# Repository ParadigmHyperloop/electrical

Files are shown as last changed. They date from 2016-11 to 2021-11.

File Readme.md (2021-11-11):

# Electrical System for the Paradigm Hyperloop Pod

## Quick Start

All boards are built using KiCad EDA (http://kicad.org/).  It is free and open source software!

1. Download and Install KiCAD
2. Clone this Repo
3. Checkout a new branch or your branch other than master
3. Open the project file (.pro) for the board you are interested in
4. Make any edits, create a branch, add and commit the changes to git, then push. 

## Organization

All files for the current revision should be kept in folders in the root directory.
All files for a completed revision should be kept in folders in the appropriate "RevX" sub-directory.
Still not sure how we will handle when some boards need to be revved but not others...

## Ops Roadmap

There are a number of nice-to-have features that will streamline the electrical workflow of board
design. The following features employ a CI server that minicks some of the features that the software
team enjoys in their git workflow.

- Automatic DRC when the PR is opened. Gate PRs on passing DRC.
- Whenever A new PR is merged to `master`, a bot will pull `master` and do the following, and commit the changes back to `master`
  - Automatic PDF export and storage in `./<board>/PDFs/`
  - Automatic BOM export and storage as `./<board>/BOM.csv`
  - Automatic SVG export and storage in `./<board>/SVG/`
  - Automatic 3D Viewer export and storage in `./<board>/3D/`
  - Automatic DRC report and storage in `./<board>/reports/`
  - Automatic export of gerbers and drill files per spec file.  Storage in `./<board>/mfg/`
  - Automatic Generation of `./board/BOT.version` containing the SHA of the commit that everything was generated for 

# License

See the [LICENSE](LICENSE) for full licensing details.

In summary, (you still need to read the whole thing), these boards are for Paradigm, 
and Paradigm only. It is shared with the world for the benefit of observers and 
potential Paradigm team members. If you wish to utilize these designs in any
way, you must contact us first and receive written permission to utilize the
designs for the purpose you require. 

We don't want to be restrictive, and we will almost certainly grant you permission,
but we want to know what you are using our designs for, and we want to make sure
you are using them correctly and safely.

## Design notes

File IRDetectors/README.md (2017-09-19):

# About this Board

* **Owner:** @edhurtig
* **Status:** `Build`
* **Topic:** Research

## Design Abstract 

In the most basic sense, this board is an Arduino with support for 2 modulated IR emitters and paired receivers. They are essentially smart IR proximity sensors. 

## Purpose

These boards are intended to detect vertical strips (4" wide) that are placed every 100' on the hypertube walls. These strips are useful for navigation purposes and tell the pod where it is in the tube.

These boards are also somewhat of a prototype for a localized control module for subsystems like #brakes where a local uC receives commands from the main flight computer, but locally is the one responsible for controlling the state of the brake control solenoids, monitoring pressures and temperatures, etc.

## Tech Specs

- **Microcontroller** Atmega32U4
- **Communication** 1 Micro USB, 1 ISP Header, 1 RS485 bus, I2C, (maybe) CANbus
- **Sensors** 2 IR Emitters, 2 IR Receivers. Local hardware-based 36Khz IR modulator.
- **Expansion Headers** All unused Atmega inputs and outputs routed to an expansion header

### RS485 Details
There are 3 ports that all share the RS485 connection: 2x Ethernet jacks (for daisy chain), 1x 4 pin Phoenix contact port

### Power Details

This board is a 5V logic level board. The board may be powered over USB or via an external power source. The external power source is recommended at 5.5V. Do not exceed 12V on any of the external power inputs.

### External Power Inputs

Power may be supplied through the 2 pin Phoenix Contact Power Connector as labeled on the board's silkscreen.

Alternatively, power may be supplied via the RJ45 jacks by supplying 5.5-12V on pin 8, and Ground on pin 7.  The jumpers for VCOM power and VCOM GND must be stuffed in order to enable power via the Ethernet ports.

**Do not plug these boards into a standard ethernet switch, behavior is undefined**

### On-Board Documentation (Silkscreen)
```
5V Logic
VCC Regulated 5V
VCOM Recommended 5.5V

Ethernet Pinout:
1-2: RS485 RX - / +
3: External IR Sync
4-5: RS485 TX - / +
6: Passthrough
7: VCOM - (Ground)
8: VCOM + (5-12V DC)

VCOM PWR set jumpers 
GND EN & VCOM EN 
```
## Status

- **Rev 1A** was ordered and lost in transit 😢 
- **Rev 1B** was ordered and partially assembled. The first board is currently in a state were it powers on. Next step is to plug in an ISP and flash a bootloader onto the Atmega.

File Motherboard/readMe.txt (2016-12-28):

Notes for Motherboard files.

*** Schematic ***
BBB headers will be shown true to pins because pinouts are not 
   set and updating the headers will be annoying.

Signals for MUX pins will be denoted with labels instead of wire 
   connections for flexibility and cleanliness.     

*** hyperLib ***
A and B designator for CD74HC4067 designate pinout orientation
   A is true to the physical pins, B is to show purpose/flow.

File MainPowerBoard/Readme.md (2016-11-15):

# Main Power Board
This board provides approriate conversion of power from 120/240VAC and 37V nominal battery packs and distribution to both 24V and 5V system loads (all loads).

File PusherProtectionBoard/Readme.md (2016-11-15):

# Emergency Power Board
This board is placed near the backup battery pack. It's purpose is, in the case of a full electrical system failure, to drain the high pressure line, confirm it is drained, and activate the emergency brakes if the pod is not currently being pushed.

## Interface
The inputs to this board are the transducer for the high pressure line (wired in parallel to its connection to BBB), the combined battery voltage from the Main Power Board, and the sensor for when the pusher is pushing (from the push plate on the rear of the pod). The outputs are a connection to the high pressure solenoid and connections to the e-brake solenoids.

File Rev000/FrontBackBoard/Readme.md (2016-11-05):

# Front/Back Board of Pod

One board is duplicated in both locations, in an effort to distribute the power system

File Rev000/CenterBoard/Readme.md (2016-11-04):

# Center Board of Pod

This board houses the main power management system, taking in 36V from the battery and distributing 24V and 5V rails to other boards throughout the pod

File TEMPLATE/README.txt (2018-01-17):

README:
I have not found a convenient way to save and load template field names for components. 
for now do the following: open kiCAD -> preferences -> Template Field Names. Then add:

Manufacturer
MFG. P/N
Vendor
Vendor P/N
Tolerance (%)

All default values should be blank, except DigiKey. 
All should be invisible except Tolerance

*Change your default text size to 41 mil

****
To load the template into the test project:
click on the Page settings via GUI or file->page settings. Click 
"browse" at the bottom and find the .wks file.

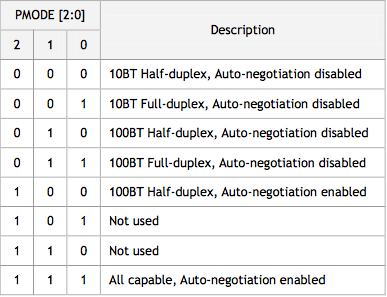
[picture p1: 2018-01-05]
Node/W5500_PMODE_settings.png

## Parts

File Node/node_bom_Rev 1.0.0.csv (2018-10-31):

Component | Description | Part | References | Value | Footprint | Quantity Per PCB | Datasheet | Digikey P/N | Mfg. Part Num | Vendor Part Num | Vendor Name | Mfg. Name | Vendor | Vendor P/N | MFG. P/N | Manufacturer | Package | MP | Stuffing | Tolerance | Manufacturer P/N | Mfr P/N
1 |  | C_small | C909 C1502 C1505 C1507 C1508 C1509 C1510 C1512 C1513 C1515 C1516 | 0.1uF | C_0805_HandSoldering | 11
2 |  | C | C205 C219 C220 C221 C222 C223 C224 C1305 C1307 C1308 C1401 C1403 C1404 C1518 C1520 C1521 C1601 C1603 C1604 C1702 C1708 C1710 C1711 C1801 C1803 C1804 C2304 C2305 C2308 C2310 | 100nF | C_0805_HandSoldering | 30 |  | 311-1088-1-ND
3 |  | C_large | C405 C506 | 100nF | C_0805_HandSoldering | 2 |  |  | GMK212BJ104KGHT | 587-3364-1-ND | Digi-Key | Taiyo Yuden
4 |  | C_small | C1503 C1506 | 100uF | C_0805_HandSoldering | 2
5 |  | C | C209 C210 | 10nF | C_0805_HandSoldering | 2
6 |  | C_large | C505 | 10pF | C_0805_HandSoldering | 1 |  |  | C0805C100K5GACTU | 399-7975-1-ND | Digi-Key | Kemet
7 |  | C | C218 C2302 C2309 | 10uF | C_0805_HandSoldering | 3
8 |  | C_small | C902 | 10uF | C_0805_HandSoldering | 1
9 |  | C_large | C504 | 12nF | C_0805_HandSoldering | 1 |  |  | CL21B123KBANNNC | 1276-2454-1-ND | Digi-Key | Samsung
10 |  | C_small | C905 | 150pF | C_0805_HandSoldering | 1
11 |  | C | C2303 C2307 | 15pF | C_0805_HandSoldering | 2
12 |  | C_large | C602 C702 | 15pF | C_0805_HandSoldering | 2 |  |  | CC0805JRNPO9BN150 | 311-1101-1-ND | Digi-Key | Yageo
13 |  | C | C202 C203 | 18pF | C_0805_HandSoldering | 2
14 |  | C | C1201 C1306 C1402 C1519 C1602 C1707 C1709 C1802 | 1uF | C_0805_HandSoldering | 8 |  | 1276-1946-1-ND
15 |  | C_large | C508 C601 C603 C701 C703 | 1uF | C_0805_HandSoldering | 5 |  |  | GRT21BC81E105KE13L CC0805KRX5R7BB105 | 490-12351-1-ND 311-3427-1-ND | Digi-Key | Murata Yageo
16 |  | C_small | C901 C903 C904 C906 C907 C908 | 1uF | C_0805_HandSoldering | 6
17 |  | C_large | C401 | 2.2uF | C_1206_HandSoldering | 1 |  |  | C3216X7S2A225K160AB | 445-5207-1-ND | Digi-Key | TDK
18 |  | C_large | C501 C502 | 2.2uF | C_0805_HandSoldering | 2 |  |  | C2012X7R1H225K125AC | 445-5968-1-ND | Digi-Key | TDK
19 |  | C_large | C404 | 2.4nF | C_0805_HandSoldering | 1 |  |  | GRM2165C1H242JA01D | 490-1629-1-ND | Digi-Key | Murata
20 |  | C_large | C402 C503 | 2.7nF | C_0805_HandSoldering | 2 |  |  | CC0805KRX7R9BB272 | 311-1130-1-ND | Digi-Key | Yageo
21 |  | C | C2301 C2306 | 22pF | C_0805_HandSoldering | 2
22 |  | C_large | C406 C407 | 22uF | C_0805_HandSoldering | 2 |  |  | C2012X5R1V226M125AC | 445-14428-1-ND | Digi-Key | TDK
23 |  | C | C2201 | 4.5nF | C_0805_HandSoldering | 1
24 |  | C | C211 | 4.7uF | C_0805_HandSoldering | 1
25 |  | C_large | C507 | 47uF | C_1206_HandSoldering | 1 |  |  | CL31A476MPHNNNE | 1276-3063-1-ND | Digi-Key | Samsung
26 |  | C | C207 C208 | 6.8nF | C_0805_HandSoldering | 2
27 |  | C_large | C403 | 82pF | C_0805_HandSoldering | 1 |  |  | CL21C820JB61PNC | 1276-2695-1-ND | Digi-Key | Samsung
28 |  | C | C1001 C1002 C1003 C1004 C1101 C1102 C1301 C1302 C1303 C1304 | C | C_0805_HandSoldering | 10
29 |  | C_large | C604 C704 | C | C_0805_HandSoldering | 2
30 |  | D_Zener_ALT | D404 | 20V | D_SOD-323_HandSoldering | 1 |  |  | MM3Z20VT1G | MM3Z20VT1GOSCT-ND |  | ON Semi
31 |  | D_Zener_ALT | D403 | 25V | D_SOD-123 | 1 |  |  | MMSZ4710T1G | MMSZ4710T1GOSCT-ND | Digi-Key | ON Semi
32 |  | D_Zener_ALT | D702 | 3.6V | D_SOD-323_HandSoldering | 1 |  |  | MM3Z3V6T1G | MM3Z3V6T1GOSCT-ND | Digi-Key | ON Semi
33 |  | D_Zener_ALT | D503 D602 | 6V | D_SOD-123 | 2 |  |  | MMSZ5233B-TP | MMSZ5233B-TPMSCT-ND | Digi-Key | Micro
34 |  | DIODESCH | D401 | DIODESCH | D_SMC_Handsoldering | 1 |  |  | B560C-13-F | B560C-FDICT-ND | Digi-Key | Diodes
35 |  | DIODESCH | D501 | DIODESCH | D_SMB_Handsoldering | 1 |  |  | B140B-13-F | B140B-FDICT-ND | Digi-Key | Diodes
36 |  | LED | D402 D502 D601 D701 | GRN | LED_1206_HandSoldering | 4 |  |  | APT3216LZGCK | 754-1944-1-ND | Digi-Key | Kingbright
37 |  | Fuse | F1101 F1102 | Fuse | R_1206_HandSoldering | 2 |  |  | C1Q 250 | 507-1073-1-ND |  | Bel Fuse
38 |  | Fuse | F1601 | Fuse | R_1812_HandSoldering | 1 |  |  | MF-MSMF050-2CT-ND | MF-MSMF050-2 |  | Bourns
39 | Generic connector, single row, 01x02 | Conn_01x02 | J301 J1501 J1502 J1503 J1504 J1505 J1506 J1507 J1508 | CONN_01X02 | Molex_2pin_power_0010844022 | 9 |  |  |  |  |  |  | DigiKey | WM1263-ND | 0010844022 | Molex, LLC Molex LLC
40 | Generic connector, single row, 01x02 | Conn_01x02 | J302 J303 | CONN_01X02 | Pin_Header_Straight_1x02_Pitch2.54mm | 2 |  |  |  |  |  |  | DigiKey | S7000-ND | PPTC021LFBN-RC | Sullins Conn. Solutions
41 | Generic connector, single row, 01x04 | Conn_01x04 | J1509 J1510 | CONN_01X04 | Molex_4pin_power_10-84-4042 | 2 |  |  |  |  |  |  | DigiKey | WM1265-ND | 10-84-4042 | Molex Connector Corporation
42 | Generic connector, single row, 01x03 | Conn_01x03 | J1001 J1002 J1003 J1004 J1101 J1102 J1201 J1202 J1203 J1204 J1205 J1206 J1900 J1901 J1902 J1903 | Conn_01x03 | TE_3_pos_header_640456-3 | 16 |  |  | 640456-3 | A19470-ND |  | TE Connectivity
43 | Generic connector, double row, 02x01, this symbol is compatible with counter-clockwise, top-bottom and odd-even numbering schemes. | Conn_02x01 | J802 J803 | Conn_02x01 | Pin_Header_Straight_2x01_Pitch2.54mm | 2 |  |  |  |  |  |  | DigiKey | 952-2262-ND | M20-9990246 | Harwin Inc
44 | Generic connector, double row, 02x02, odd/even pin numbering scheme (row 1 odd numbers, row 2 even numbers) | Conn_02x02_Odd_Even | J801 | Conn_02x02_Odd_Even | Pin_Header_Straight_2x02_Pitch2.54mm | 1 |  |  |  |  |  |  | DigiKey | 609-3242-ND | 67997-404HLF | Amphenol FCI
45 | Generic connector, double row, 02x03, odd/even pin numbering scheme (row 1 odd numbers, row 2 even numbers) | Conn_02x03_Odd_Even | J1601 | Conn_02x03_Odd_Even | Pin_Header_Straight_2x03_Pitch2.54mm | 1 |  |  |  |  |  |  | DigiKey | S9015E-03-ND | GRPB032VWVN-RC | Sullins Conn. Solutions
46 | Generic connector, double row, 02x05, odd/even pin numbering scheme (row 1 odd numbers, row 2 even numbers) | Conn_02x05_Odd_Even | J2201 | Conn_02x05_Odd_Even | Pin_Header_Straight_2x05_Pitch1.27mm | 1 |  |  |  |  |  |  | DigiKey | 609-3712-ND | 20021111-00010T4LF | Amphenol FCI
47 |  | RB1-125BAG1A | J201 | RB1-125BAG1A | WIZNET_RB1-125BAG1A | 1 | 2.18 USD |  | RB1-125BAG1A |  |  | WIZnet |  |  |  |  | HVQFN-36 NXP Semiconductors | RB1-125BAG1A
48 | USB Micro Type B connector | USB_B_Micro | J1602 | USB_B_Micro | USB_Micro-B_10103594-0001LF | 1 |  |  | 609-4050-1-ND | 10103594-0001LF |  | Amphenol
49 |  | L_large | L401 | 33uH | Wurth_inductor_7443551331 | 1 |  |  | 7443551331 | 732-3881-1-ND | Digi-Key | Wurth Electronics
50 |  | L_large | L501 | 33uH | Bourns_33uH_inductor_SRR6028-330Y | 1 |  |  | SRR6028-330Y | SRR6028-330YCT-ND | Digi-Key | Bourns
51 |  | Ferrite_Bead_Small | L201 L202 L2301 | Ferrite_Bead_Small | R_1206_HandSoldering | 3
52 |  | L_small | L601 L701 | INDUCTOR_SMALL | R_1206_HandSoldering | 2 |  |  | RC1206JR-070RL | 311-0.0ERCT-ND |  | Yageo
53 |  | R | R202 R1001 R1002 R1003 R1004 R1009 R1010 R1011 R1012 R1021 R1022 R1023 R1024 R1101 R1102 R1301 R1302 R1303 R1304 R1308 R1404 R1513 R1604 R1706 R1804 R2202 R2203 R2204 R2205 R2206 R2207 R2208 R2209 R2308 R2309 R2310 R2311 R2312 R2313 R2314 R2315 R2316 R2317 R2318 R2319 R2320 R2321 R2322 R2323 R2324 R2325 R2326 R2327 R2328 | 0 | R_0805_HandSoldering | 54
54 |  | R_large | R403 R501 R506 R1502 R1503 R1504 R1505 R1507 R1508 R2001 R2101 R2102 R2103 R2104 R2105 R2106 R2107 R2108 | 0 | R_0805_HandSoldering | 18 |  |  | RC0805JR-070RL | 311-0.0ARCT-ND | Digi-Key | Yageo |  |  |  |  |  |  | NOSTUFF
55 |  | R | R201 | 0 | R_1206_HandSoldering | 1
56 |  | R_small | R902 | 0 | R_0805_HandSoldering | 1
57 |  | R_large | R604 | 1.2k | R_0805_HandSoldering | 1 |  |  | RC0805JR-071K2L | 311-1.2KARCT-ND | Digi-Key | Yageo
58 |  | R_large | R507 | 1.4k | R_0805_HandSoldering | 1 |  |  | RC0805FR-071K4L | 311-1.40KCRCT-ND | Digi-Key | Yageo
59 |  | R-RESCUE-node | R204 | 10 | R_0805_HandSoldering | 1 |  |  |  |  |  |  |  |  |  |  |  |  |  | 1%
60 |  | R_small | R904 | 100 | R_0805_HandSoldering | 1
61 |  | R_large | R903 R905 R906 | 100k | R_0805_HandSoldering | 3 |  |  |  |  |  |  | DigiKey
62 |  | R_large | R301 | 100m | R_2512_HandSoldering | 1 |  |  | CRA2512-FZ-R100ELF | CRA2512-FZ-R100ELFCT-ND |  | Bourns
63 |  | R | R221 R1017 R1018 R1019 R1020 R1701 | 10K | R_0805_HandSoldering | 6
64 |  | R-RESCUE-node | R210 R214 R215 R216 R217 R218 R219 R222 R223 R224 | 10K | R_0805_HandSoldering | 10
65 |  | R_large | R503 R601 R701 R1501 R1506 | 10k | R_0805_HandSoldering | 5 |  |  |  |  | Digi-Key
66 |  | R_large | R508 | 11.3k | R_0805_HandSoldering | 1 |  |  |  |  | Digi-Key |  | DigiKey | 311-11.3KCRCT-ND | RC0805FR-0711K3L | Yageo |  |  |  | 1%
67 |  | R_large | R401 | 11.5k | R_0805_HandSoldering | 1 |  |  |  |  | Digi-Key |  | DigiKey | 311-11.5KCRCT-ND | RC0805FR-0711K5L | Yageo |  |  |  | 1%
68 |  | R | R228 | 12.4K | R_0805_HandSoldering | 1 |  |  | RC0805FR-0712K4L | 311-12.4KCRCT-ND |  | Yageo |  |  |  |  |  |  |  | 1%
69 |  | R_large | R502 | 124k | R_0805_HandSoldering | 1 |  |  | RC0805FR-07124KL | 311-124KCRCT-ND | Digi-Key | Yageo
70 |  | R | R1306 R1307 R1402 R1403 R1511 R1512 R1602 R1603 R1704 R1705 R1802 R1803 | 150 | R_0805_HandSoldering | 12 |  | 311-150HRCT-ND
71 |  | R_large | R2002 | 150 | R_0805_HandSoldering | 1
72 |  | R_large | R2003 R2004 | 15k | R_0805_HandSoldering | 2
73 |  | R_large | R504 | 17.4k | R_0805_HandSoldering | 1 |  |  | RC0805FR-0717K4L | 311-17.4KCRCT-ND | Digi-Key | Yageo
74 |  | R | R203 R1305 R1401 R1510 R1601 R1703 R1801 R2201 | 1M | R_0805_HandSoldering | 8 |  | 311-1.00MHRCT-ND
75 |  | R | R2307 | 1k | R_0805_HandSoldering | 1
76 |  | R | R1104 R1106 | 20k | R_0805_HandSoldering | 2
77 |  | R_large | R402 | 210k | R_0805_HandSoldering | 1 |  |  | RC0805FR-07210KL | 311-210KCRCT-ND | Digi-Key | Yageo
78 |  | R | R1005 R1006 R1007 R1008 | 250 | R_0805_HandSoldering | 4
79 |  | R_large | R404 | 27.4k | R_0805_HandSoldering | 1 |  |  | RC0805FR-0727K4L | 311-27.4KCRCT-ND | Digi-Key | Yageo
80 |  | R_large | R603 R703 | 29.4k | R_0805_HandSoldering | 2 |  |  |  |  | Digi-Key |  | DigiKey | 311-29.4KCRCT-ND | RC0805FR-0729K4L | Yageo |  |  |  | 1%
81 |  | R | R207 R208 R220 R225 | 33 | R_0805_HandSoldering | 4 |  |  | RC0805FR-0733RL | 311-33.0CRCT-ND |  | Yageo
82 |  | R | R1702 | 330 | R_0805_HandSoldering | 1
83 |  | R-RESCUE-node | R209 R211 | 330 | R_0805_HandSoldering | 2
84 |  | R_large | R704 | 330 | R_0805_HandSoldering | 1 |  |  | RC0805JR-07330RL | 311-330ARCT-ND | Digi-Key | Yageo
85 |  | R_large | R405 | 348k | R_0805_HandSoldering | 1 |  |  |  |  | Digi-Key |  | DigiKey | 311-348KCRCT-ND | RC0805FR-07348KL | Yageo |  |  |  | 1%
86 |  | R | R1013 R1014 R1015 R1016 | 40k | R_0805_HandSoldering | 4
87 |  | R | R1201 | 45k | R_0805_HandSoldering | 1 |  |  |  |  |  |  | DigiKey | 311-.05SCT-ND
88 |  | R | R205 R206 R212 R213 | 49.9 | R_0805_HandSoldering | 4 |  |  | RC0805FR-0749R9L | 311-49.9CRCT-ND |  | Yageo |  |  |  |  |  |  |  | 1%
89 |  | R | R907 | 50K | R_0805_HandSoldering | 1 |  |  |  |  |  |  | DigiKey
90 |  | R_large | R702 | 51k | R_0805_HandSoldering | 1 |  |  | RC0805FR-0751KL | 311-51.0KCRCT-ND | Digi-Key | Yageo | DigiKey | 311-51.0KCRCT-ND | RC0805FR-0751KL | Yageo |  |  |  | 1%
91 |  | R | R1202 | 5k | R_0805_HandSoldering | 1 |  |  |  |  |  |  | DigiKey | 311-5.1KJRCT-ND
92 |  | R_large | R901 | 5k | R_0805_HandSoldering | 1 |  |  |  |  |  |  | DigiKey
93 |  | R_large | R505 | 66.5k | R_0805_HandSoldering | 1 |  |  | ERJ-6ENF6652V | P66.5KCCT-ND | Digi-Key | Panasonic | DigiKey | 311-66.5KCRCT-ND | RC0805FR-0766K5L | Yageo |  |  |  | 1%
94 |  | R_large | R406 | 698 | R_0805_HandSoldering | 1 |  |  | RC0805FR-07698RL | 311-698CRCT-ND | Digi-Key | Yageo
95 |  | R | R1103 R1105 | 82k | R_0805_HandSoldering | 2
96 |  | R_large | R602 | 93.1k | R_0805_HandSoldering | 1 |  |  | RC0805FR-0793K1L | 311-93.1KCRCT-ND | Digi-Key | Yageo | DigiKey | 311-93.1KCRCT-ND | RC0805FR-0793K1L | Yageo |  |  |  | 1%
97 |  | SW_Push | SW1701 | SW_Push | C&K_switch_PTS645SM43SMTR92 | 1 |  |  |  |  |  |  | DigiKey | CKN9112CT-ND | PTS645SM43SMTR92 LFS | C&K
98 |  | AD849X | U1301 U1401 U1508 U1601 U1702 U1801 | AD849X | MSOP-8_3x3mm_Pitch0.65mm | 6 | http://www.analog.com/media/en/technical-documentation/data-sheets/AD8494_8495_8496_8497.pdf |  |  |  |  |  | DigiKey | AD8495ARMZ-R7CT-ND |  | Analog Devices |  |  |  |  | AD8495ARMZ-R7
99 |  | ADS7953_38TSSOP | U901 | ADS7953 | TSSOP-38_4.4x9.7mm_Pitch0.5mm | 1 |  |  |  |  |  |  | DigiKey
100 |  | BTS4300SGA | U2001 | BTS4300SGA | SOIC-8_3.9x4.9mm_Pitch1.27mm | 1 |  |  | BTS4300SGAXUMA1 | BTS4300SGAXUMA1CT-ND |  | Infineon
101 |  | DAC7760 | U1503 U1504 | DAC7760 | HTSSOP-24_7.8x4.4mm_Pitch0.65mm_ThermalPad | 2 | http://www.ti.com/lit/ds/symlink/dac7760.pdf |  |  |  |  |  | DigiKey | 296-37188-1-ND |  | Texas Instruments |  |  |  |  | DAC7760IPWPR
102 |  | DRV8806 | U1501 U1502 | DRV8806 | TSSOP-16-1EP_4.4x5mm_Pitch0.65mm | 2 |  |  | DRV8806PWPR | 296-34887-1-ND |  | Texas Instruments
103 |  | IC_MICROCHIP_SAMD21G18A-A | U1701 | IC_MICROCHIP_SAMD21G18A-A | TQFP-48_7x7mm_Pitch0.5mm | 1 |  |  |  |  |  |  | DigiKey | ATSAMD21G18A-AUTCT-ND | ATSAMD21G18A-AUT | Microchip Technology
104 |  | LM358 | U1001 U1002 | LM358 | SOIC-8_3.9x4.9mm_Pitch1.27mm | 2 |  |  | LM358ADR |  | 296-14601-1-ND | Texas Instruments
105 |  | IC_TexasInstruments_Sequencer | U903 | LM3880 | SOT-23-6_Handsoldering | 1 |  |  |  |  |  |  | DigiKey | LM3880MF-1AA/NOPBCT-ND |  | Texas Instruments |  |  |  |  | LM3880MF-1AA/NOPB
106 |  | IC_Texas_Intruments_LM4132_LDO-REF | U904 | LM4132 | SOT-23-5 | 1 |  |  |  |  |  |  | DigiKey | LM4132BMF-2.5/NOPBCT-ND |  | Texas Instruments |  |  |  |  | LM4132BMF-2.5/NOPB
107 |  | LMV601 | U1201 | LMV601 | SOT-363_SC-70-6_Handsoldering | 1 |  |  |  |  |  |  | DigiKey | 296-39050-1-ND |  | Texas Instruments |  |  |  |  | LMV601MG/NOPB
108 |  | OPA172 | U1505 U1506 | OPA172 | SOT-23-5 | 2 |  |  |  |  |  |  | DigiKey | 296-40433-1-ND | OPA172IDBVR | Texas Instruments
109 |  | IC_Texas_Instruments_OPA192 | U902 | OPA192 | SOT-23-5 | 1 |  |  |  |  |  |  | DigiKey | 296-42105-1-ND |  | Texas Instruments |  |  |  |  |  | OPA192IDBVR
110 |  | TLV71333PDBV | U905 | TLV71333 | SOT-23-5 | 1 |  |  | TLV71333PDBV |  |  |  | DigiKey | 296-35591-1-ND |  | Texas Instruments
111 |  | TPS54361 | U401 U501 | TPS54361 | TI_buckreg_TPS54361DPRR | 2 | http://www.ti.com/lit/ds/symlink/tps54361.pdf |  | TPS54361DPRR | 296-40794-1-ND | Digi-Key | Texas Instruments
112 |  | TPS795 | U601 U701 | TPS795 | SOT-223-6 | 2 |  |  | TPS79501DCQR | 296-13806-1-ND | Digi-Key | Texas Instruments
113 |  | W5500 | U201 | W5500 | LQFP-48_7x7mm_Pitch0.5mm | 1 | DOCUMENTATION |  | W5500 | 1278-1021-ND |  | WIZnet
114 |  | POT_large | VR401 VR601 VR701 | 1k | TT_1k_potentiometer_23BR1KLFTR | 3 |  |  | 23BR1KLFTR | 490-2881-ND | Digi-Key | 987-1015-1-ND
115 |  | Varistor | VR1601 VR1602 | VR | R_0603_HandSoldering | 2 |  |  | CG0603MLC-05E | CG0603MLC-05ECT-ND | Digi-Key | Bourns
116 |  | Crystal | Y201 Y2302 | 25MHz | Murata_25MHz_XTAL_XRCGB25M000F3M00R0 | 2 |  |  | XRCGB25M000F3M00R0 | 490-5578-1-ND |  | Murata
117 |  | Crystal | Y2301 | 32.768kHz | TXC_32kHz_XTAL_9HT10-32.768KBZY-T | 1 |  |  | 9HT10-32.768KBZY-T | 887-2605-1-ND |  | TXC
Component Groups: | 119
Component Count: | 373
Fitted Components: | 369
Number of PCBs: | 1
Total components: | 369
Schematic Version: | Rev 1.0.0
Schematic Date: | 2017-09-07
BoM Date: | Wednesday, January 31, 2018 'AMt' 01:02:04 AM
Schematic Source: | /Users/lukemerkl/Desktop/electrical/Node/node.sch
KiCad Version: | Eeschema 4.0.4-stable

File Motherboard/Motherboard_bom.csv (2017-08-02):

Component | Description | Part | References | Value | Footprint | Quantity Per PCB | Datasheet | Digikey P/N | MFR P/N
1 | Resistor | Ferrite__BLM21_Murata | B301 | Ferrite__BLM21_Murata | R_0805_HandSoldering | 1 |  | 490-1040-1-ND | BLM21AG601SN1D
2 | Unpolarized capacitor | C | C201 C202 C1311 C1312 C1313 C1314 C1315 C1406 | 0.1uF | C_0603_HandSoldering | 8 |  | 311-1088-1-ND | CC0603KRX7R7BB104
3 | Unpolarized capacitor | C | C301 C302 C407 C408 C707 C708 C807 C808 C907 C908 C1007 C1008 C1107 C1108 C1112 C1113 | 100nF | C_0805_HandSoldering | 16 |  | 490-12557-1-ND | GRM219R71C104JA01D
4 | Unpolarized capacitor | C | C1507 | 10nF | C_0603_HandSoldering | 1 |  | 311-3369-1-ND | CC0603KRX7R7BB103
5 | Unpolarized capacitor | C | C403 C703 C803 C903 C1003 C1103 C1105 | 10uF | C_0603_HandSoldering | 7 |  | 1276-1948-1-ND | CL10B106MQ8NRNC
6 | Unpolarized capacitor | C | C1501 C1502 | 10uf | R_0805_HandSoldering | 2 |  | 490-10516-1-ND | GRM21BR71A106KA73L
7 | Unpolarized capacitor | C | C406 C706 C806 C906 C1006 C1106 C1111 | 150pF | C_0603_HandSoldering | 7 |  | 732-7753-1-ND | 885012006009
8 | Unpolarized capacitor | C | C401 C402 C404 C405 C601 C602 C603 C604 C701 C702 C704 C705 C801 C802 C804 C805 C901 C902 C904 C905 C1001 C1002 C1004 C1005 C1101 C1102 C1104 C1109 C1110 C1504 | 1uF | C_0603_HandSoldering | 30 |  | 1276-1946-1-ND | CL10B105KP8NNNC
9 | Unpolarized capacitor | C | C1508 | 2.2uF | C_0603_HandSoldering | 1 |  | 399-3522-1-ND | C0805C225K8RACTU
10 | Unpolarized capacitor | C | C204 C206 | 22pF | R_0603_HandSoldering | 2 |  | 478-6204-1-ND | 478-6204-1-ND
11 | Unpolarized capacitor | C | C303 | 4.7uF | C_0805_HandSoldering | 1 |  | 399-7415-1-ND | C0805C475K4RACTU
12 | Unpolarized capacitor | C | C203 | SAT |  | 1
13 | Unpolarized capacitor | C | C205 | SAT | R_0805_HandSoldering | 1 |  | 1276-1946-1-ND | CL10B105KP8NNNC
14 |  | LED | D1501 | AMBER_LED | LED_0805 | 1 |  | 516-1431-1-ND | HSMA-C170
15 |  | LED | D401 | BLUE_LED | LED_0805 | 1 |  | 160-1645-1-ND | LTST-C171TBKT
16 |  | LED | D601 D602 D603 D604 D605 D607 D608 D1502 D1503 D1504 | GREEN_LED | LED_0805 | 10 |  | 475-1410-1-ND | LG R971-KN-1
17 |  | LED | D302 | RX_LED | D_0805 | 1 |  | L62507CT-ND | CMD17-21VYD/TR8
18 |  | LED | D301 | TX_LED | D_0805 | 1 |  | L62507CT-ND | CMD17-21VYD/TR8
19 |  | FUSE | F301 | FUSE | R_1812_HandSoldering | 1 |  | MS-MSMF050-2CT-ND | MF-MSMF050-2
20 | PDIP28 Narrow, 16k Flash, 1kB SRAM, 512B EEPROM | ATMEGA328-P | IC201 | ATMEGA328-P | DIP-28_W7.62mm | 1 | http://www.atmel.com/images/atmel-8271-8-bit-avr-microcontroller-atmega48a-48pa-88a-88pa-168a-168pa-328-328p_datasheet.pdf | ATMEGA328P-PU-ND | ATMEGA328P-PU
21 |  | JUMPER3 | JP201 JP601 JP1501 | JUMPER3 | Wafer_Vertical10x5.8x7RM2.5-3 | 3 |  | 732-5316-ND | 61300311121
22 |  | BeagleboneBlack_P8 | P406 | BeagleboneBlack_P8 | header_2.54x2.54mm_spacing_pinName | 1 |  | S7126-ND | PPPC232LFBN-RC
23 |  | BeagleboneBlack_P9 | P405 | BeagleboneBlack_P9 | header_2.54x2.54mm_spacing_pinName | 1 |  | S7126-ND | PPPC232LFBN-RC
24 | Connector, single row, 01x01 | CONN_01X01 | P1406 | CONN_01X01 | Pin_Header_Straight_1x01_Pitch2.54mm | 1 |  | DNS
25 | Connector, single row, 01x02 | CONN_01X02 | P401 P403 P411 P1304 P1305 P1306 P1401 P1402 P1403 P1404 | CONN_01X02 | CONN_PHOENIX_1923869_2PIN | 10 |  | 277-2416-ND | 1844210
26 | Connector, single row, 01x03 | CONN_01X03 | P501 P502 P503 P504 | CONN_01X03 | 3POS_Header_TEConn_6.35mm_pitch | 4 |  | A14328-ND | 350825-1
27 | Connector, single row, 01x04 | CONN_01X04 | P402 P404 P1302 P1303 | CONN_01X04 | CONN_PHOENIX_1844236_4PIN | 4 |  | 277-2419-ND | 1844236
28 | Connector, single row, 01x06 | CONN_01X06 | P201 | CONN_01X06 | quick_6pin_2.54mm | 1 |  | 609-3263-ND | 68000-406HLF
29 | Connector, double row, 02x08 | CONN_02X08 | P1201 P1301 | CONN_02X08 | OnShore_16Pin_Vert_2.54mm_spacing | 2 |  | ED10523-ND | 302-S161
30 | Connector, double row, 02x23 | CONN_02X23 | P407 P408 P409 P410 | CONN_02X23 | header_2.54x2.54mm_spacing_pinName | 4 |  | S2012EC-23-ND | PREC023DAAN-RC
31 | Mating connector | CONN_02X25 | P701 P801 P901 P1101 | CONN_02X25 | 3M_50pos_latching | 4 |  | MHS50N | N3433-6302RB
32 | USB micro/mini connector | USB_OTG | P301 | USB_OTG | USB_Mini-B | 1 |  | 609-4700-1-ND | 10033526-N3212LF
33 | Resistor | R | R307 R406 R407 R408 R409 R410 R606 R609 R610 R611 R701 R702 R703 R704 R707 R801 R802 R803 R804 R807 R901 R902 R903 R904 R907 R1005 R1006 R1007 R1008 R1009 R1101 R1102 R1103 R1104 R1106 R1107 R1413 | 0 | R_0805_HandSoldering | 37 |  | 311-0.0ARTR-ND | RC0805JR-070RL
34 | Resistor | R | R1301 R1302 R1306 R1308 R1309 R1310 R1311 R1312 R1313 R1314 | 1.5k | R_0603_HandSoldering | 10 |  | 311-1.5KGRCT-ND | RC0603JR-071K5L
35 | Resistor | R | R411 R705 R805 R905 R1010 R1105 R1108 | 100 | R_0603_HandSoldering | 7 |  | 311-100HRCT-ND | RC0603FR-07100RL
36 | Resistor | R | R1505 R1506 R1507 | 100k | R_0805_HandSoldering | 3 |  | 311-100KCRCT-ND | RC0805FR-07100KL
37 | Resistor | R | R204 R303 R306 R401 R402 R405 | 10K | R_0805_HandSoldering | 6 |  | 311-10KARCT-ND | RC0805JR-0710KL
38 | Resistor | R | R403 R404 | 15k | R_0805_HandSoldering | 2 |  | 311-10KARCT-ND | RC0805JR-0710KL
39 | Resistor | R | R301 R302 | 22 | R_0603_HandSoldering | 2 |  | 311-22GRCT-ND | RC0603JR-0722RL
40 | Resistor | R | R304 R305 | 270 | R_0805_HandSoldering | 2 |  | 311-270GRCT-ND | RC0603JR-07270RL
41 | Resistor | R | R1501 R1502 R1504 | 300 | R_0805_HandSoldering | 3 |  | 311-300ARCT-ND | RC0805JR-07300RL
42 | Resistor | R | R1503 | 300 | R_0603_HandSoldering | 1 |  | 311-300GRCT-ND | RC0603JR-07300RL
43 | Resistor | R | R601 R602 R603 R604 R605 R607 R608 | 590 | R_0805_HandSoldering | 7 |  | 311-590HRCT-ND | RC0603FR-07590RL
44 | Resistor | R | R101 R102 R103 R104 R706 R708 R709 R710 R806 R808 R809 R810 R906 R908 R909 R910 R1001 R1002 R1003 R1004 | SAT | R_0805_HandSoldering | 20
45 | Button | SW_PUSH | SW201 SW301 | SW_PUSH | SW_SPST_B3S-1000 | 2 |  | SW836CT-ND | B3S-1000P | B3S-1000P
46 | point | TEST_1P | T201 T202 | TEST_1P | Measurement_Point_Round-TH_Big | 2 |  | 36-5001-ND | 5001
47 |  | ADS7953_38TSSOP | U701 U801 U901 U1101 U1201 U1301 | ADS7953_38TSSOP | TSSOP-38_4.4x9.7mm_Pitch0.5mm | 6 |  | 296-23504-5-ND | ADS7953SBDBT
48 |  | ADS7953_38TSSOP | U501 | ADS7953_38TSSOP | TSSOP-38_4.4x9.7mm_Pitch0.5mm | 1 |  | 296-23504-5-ND | ADS7953SBDBT
49 |  | ADuM3150_AnalogDev_7CH_ISO | U1304 | ADuM3150_AnalogDev_7CH_ISO | SSOP-20_5.3x7.2mm_Pitch0.65mm | 1 |  | ADUM3150BRSZ-ND | ADUM3150BRSZ
50 |  | DEMUX_1to8_TI | U602 | DEMUX_1to8_TI | TSSOP-16-1EP_4.4x5mm_Pitch0.65mm | 1 |  | 296-1223-1-ND | SN74LVC138APWR
51 | USB to Serial Interface, SSOP-28 | FT232RL | U301 | FT232RL | SSOP-28_5.3x10.2mm_Pitch0.65mm | 1 | http://www.ftdichip.com/Products/ICs/FT232RL.htm | 768-1007-1-ND | FT232RL-REEL
52 |  | I2C_ISO_TI_ISO1540 | U1402 U1403 | I2C_ISO_TI_ISO1541 | SOIC-8_3.9x4.9mm_Pitch1.27mm | 2 |  | 296-34872-1-ND | ISO1541DR
53 |  | LEVEL_SHIFT_NXP_14TSSOP | U401 | LEVEL_SHIFT_NXP_14TSSOP | TSSOP-14_4.4x5mm_Pitch0.65mm | 1 |  | 568-8382-1-ND | NTS0104PW,118 | NTS0104PW,118
54 |  | LM3880_TexasInstruments_PWR_SEQ | U1504 | LM3880_TexasInstruments_PWR_SEQ | SOT-23-6_Handsoldering | 1 |  | 296-43848-1-ND | LM3880MFX-1AA/NOPB
55 |  | LM4132_TexasInstruments__LDO_REF | U403 U703 U803 U903 U1002 U1103 U1105 | LM4132_TexasInstruments__LDO_REF | SOT-23-5_HandSoldering | 7 |  | LM4132EMF-2.5/NOPBCT-ND | LM4132EMF-2.5/NOPB
56 |  | LP2985-N | U1503 | LP2985-N | SOT-23-5_HandSoldering | 1 |  | 296-18476-1-ND | LP2985-33DBVR
57 | 1A Low drop-out regulator, Adjustable Output 1.25 - 18.8V, SOT223 | NCP1117ST50T3G_MountingTab | U1501 | NCP1117ST50T3G_MountingTab | SOT-223 | 1 | http://www.onsemi.com/pub_link/Collateral/NCP1117-D.PDF | NCP1117ST50T3GOSCT-ND | NCP1117ST50T3G
58 | Op Amp in 5-pin package | OPA656 | U402 U702 U802 U902 U1001 U1102 U1104 | OPA192 | SOT-23-5_HandSoldering | 7 | http://www.ti.com/lit/gpn/opa376 | 296-42105-1-ND | OPA192IDBVR
59 |  | TPS719XX_TexasInstruments_2x2SON | U1502 | TPS719XX_TexasInstruments_2x2SON | TPS719XX_TexasInstruments_2x2_mm_SON | 1 |  | 296-21662-1-ND | TPS71933-33DRVR
60 | VARISTANCE | VR | VR301 VR302 | 5V | R_0603_HandSoldering | 2 |  | CG0603MLC-05LECT-ND | CG0603MLC-05LE
61 | Two pin crystal | Crystal | Y201 | 16MHz | Crystal_HC49-U_Vertical | 1 |  | X1103-ND | ECS-160-20-4X
Component Groups: | 61
Component Count: | 268
Fitted Components: | 268
Number of PCBs: | 1
Total components: | 268
Schematic Version: | 2.1.0
Schematic Date: | 7/31/2017
BoM Date: | 8/2/2017 7:25
Schematic Source: | C:/Users/Luke Merkl/Desktop/electrical/Motherboard/Motherboard.sch
KiCad Version: | Eeschema 4.0.4-stable

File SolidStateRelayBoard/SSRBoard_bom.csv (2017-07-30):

Component | Description | Part | References | Value | Footprint | Quantity Per PCB | Datasheet | Mfr PN | Link | Digikey PN | URL | Mfg. | Mfg. PN | site | website
1 | Unpolarized capacitor | C | C104 C105 C106 C107 C108 | 0.1uF | C_0805_HandSoldering | 5 |  | 08055C104KAT2A | https://www.digikey.com/product-detail/en/avx-corporation/08055C104KAT2A/478-1395-1-ND/564427 | 478-1395-1-ND
2 | Unpolarized capacitor | C | C101 C102 C103 | 10nF | C_1206_HandSoldering | 3 |  |  |  | 399-14845-6-ND | https://www.digikey.com/product-detail/en/kemet/C1206C103JCGACAUTO/399-14845-6-ND/7364194 |  |  |  |  | 5=.02R
3 |  | ZENER-RESCUE-SSRBoard | D201 D301 D401 D501 D601 D701 D801 D901 D1001 D1101 D1201 D1301 D1401 | 5.6V | SOD-123 | 13 |  |  |  | MMSZ5232B-FDICT-ND |  | Diodes | MMSZ5232B-7-F
4 |  | LED-RESCUE-SSRBoard | D202 D302 D402 D502 D602 D702 D802 D902 D1002 D1102 D1202 D1302 D1402 | LED | SOD-123 | 13 |  |  |  | 754-1939-1-ND |  | Kingbright | APT2012LZGCK
5 | LED generic | LED | D101 | LED | LED_0805_HandSoldering | 1 |  |  |  | 475-1410-2-ND
6 | Connector, single row, 01x02, pin header | CONN_01X02 | J101 J102 J103 J104 J105 J106 J107 J108 J109 J110 J111 J112 J113 J117 J118 J119 J120 J121 J122 J123 J124 J125 J126 J127 J128 J129 J134 P110 P111 P112 | CONN_01X02 | CONN_PHOENIX_1844210_2PIN | 30 |  |  |  | 277-2416-ND |  | Phoenix | 1844210
7 | Connector, single row, 01x04, pin header | CONN_01X04 | J114 J115 J116 P101 | CONN_01X04 | CONN_PHOENIX_1844236_4PIN | 4 |  |  |  | 277-2419-ND
8 |  | JUMPER | JP101 JP102 JP103 JP104 JP105 JP106 JP107 JP108 JP109 JP110 JP111 JP112 JP113 JP114 JP115 | JUMPER | R_2512_HandSoldering | 15 |  |  |  | RMCF2512ZT0R00CT-ND |  | Stackpole | RMCF2512ZT0R00
9 | Connector, single row, 01x03, pin header | CONN_01X03 | P105 P106 P107 P108 P109 | Addressing | TO-220-3_Vertical | 5
10 | Connector, single row, 01x01, pin header | CONN_01X01 | P201 P301 P401 P501 P601 P701 P801 P901 P1001 P1101 P1201 P1301 P1401 | CONN_01X01 | 1pin | 13 |  |  |  | 36-5000-ND
11 |  | MMBT2222ALT1G | Q201 Q301 Q401 Q501 Q601 Q701 Q801 Q901 Q1001 Q1101 Q1201 Q1301 Q1401 | MMBT2222ALT1G | SOT-23_Handsoldering | 13 |  |  |  | MMBT2222ALT1GOSCT-ND |  | ON Semi | MMBT2222ALT1G
12 | Transistor P-MOSFET with substrate diode (general) | Q_PMOS_DGS_SSR | Q101 Q102 Q105 | Q_PMOS_DGS_SSR | SOT-223-3Lead_TabPin2 | 3 |  |  |  | NTF2955T1GOSTR-ND
13 | Transistor PNP (general) | Q_PNP_BEC | Q103 Q104 Q106 | Q_PNP_BEC | SOT-23_Handsoldering | 3 |  |  |  | MMBT5087CT-ND |  |  |  | https://www.digikey.com/products/en?keywords=MMBT5087CT-ND
14 | Resistor | R | R101 R102 R103 R104 R105 R106 R107 R108 R109 R110 R111 R112 R113 R114 R115 R116 R117 | 0 | R_1206_HandSoldering | 17 |  |  |  | P0.0ECT-ND
15 | Resistor | R | R124 R125 R128 R134 | 0 | R_0805_HandSoldering | 4 |  |  |  | P0.0ATR-ND
16 |  | R-RESCUE-SSRBoard | R201 R301 R401 R501 R601 R701 R801 R901 R1001 R1101 R1201 R1301 R1401 | 10k | R_1206_HandSoldering | 13 |  |  |  | 311-10.0KFRCT-ND |  | Yageo | RC1206FR-0710KL
17 | Resistor | R | R118 R119 R120 R121 R122 R123 | 15 | R_0805_HandSoldering | 6 |  |  |  | P15ATR-ND |  |  |  |  | https://industrial.panasonic.com/ww/products/resistors/chip-resistors/general-purpose-chip-resistors/thick-film-chip-resistors/ERJ6GEYJ150V
18 |  | R-RESCUE-SSRBoard | R202 R302 R402 R502 R602 R702 R802 R902 R1002 R1102 R1202 R1302 R1402 | 1M | R_1206_HandSoldering | 13 |  |  |  | 311-1.0MERCT-ND |  | Yageo | RC1206JR-071ML
19 | Resistor | R | R130 R131 R132 | 20K | R_0805_HandSoldering | 3 |  |  | https://www.digikey.com/product-detail/en/panasonic-electronic-components/ERJ-6GEYJ203V/P20KATR-ND/83076 | P20KATR-ND
20 | Resistor | R | R126 R127 R129 | 2k | R_0805_HandSoldering | 3 |  |  |  | P2.00KCTR-ND
21 | Resistor | R | R135 R136 | 5K | R_0805_HandSoldering | 2 |  |  |  | Y1629-5.0KATR-ND
22 |  | R-RESCUE-SSRBoard | R203 R204 R303 R304 R403 R404 R503 R504 R603 R604 R703 R704 R803 R804 R903 R904 R1003 R1004 R1103 R1104 R1203 R1204 R1303 R1304 R1403 R1404 | 910 | R_1206_HandSoldering | 26 |  |  |  | 311-910FRCT-ND |  | Yageo | RC1206FR-07910RL
23 | Resistor | R | R133 | R | C_0805_HandSoldering | 1 |  |  |  | RMCF0805JT330RTR-ND
24 |  | LEDDriverSSR | U101 | LEDDriverSSR | TSSOP-28_4.4x9.7mm_Pitch0.65mm | 1 |  |  | https://www.digikey.com/products/en?keywords=568-5931-1-ND | 568-5931-1-ND
25 |  | SSR | U201 U301 U401 U501 U601 U701 U801 U901 U1001 U1101 U1201 U1301 U1401 | SSR | VISHAY_6SMD_OPTOCOUPLER | 13 |  |  |  | VO14642AABCT-ND |  | Vishay | VO14642AABTR
26 |  | XTR111 | U102 U103 U104 | XTR111 |  | 3 | http://www.ti.com/lit/ds/symlink/xtr111.pdf |  |  | 296-39545-2-ND
Component Groups: | 26
Component Count: | 226
Fitted Components: | 226 |  |  |  |  |  |  |  |  | Y1629-5.0KATR-ND
Number of PCBs: | 1
Total components: | 226
Schematic Version:
Schematic Date:
BoM Date: | Friday, July 14, 2017 'PMt' 01:17:50 PM
Schematic Source: | /Users/chrisreusch/Documents/Hyperloop/full_electrical/SolidStateRelayBoard/SSRBoard.sch
KiCad Version: | Eeschema 4.0.6

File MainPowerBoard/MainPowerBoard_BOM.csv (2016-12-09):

Id | Designator | Package | Quantity | Designation | Supplier and ref
1 | J107 | CONN_PHOENIX_1844252_6PIN | 1 | CONN_01X06
2 | U704 | SOIC-8_3.9x4.9mm_Pitch1.27mm | 1 | TLC393
3 | U702 | SOT-23-5 | 1 | TLV271IDBVR
4 | TP401,TP402,TP403,TP603,TP602,TP601,TP503,TP502,TP501 | TP_SMT_Keystone | 9 | Testpoint
5 | F401,F601,F501 | SCHURTER_0031_3804_FUSE | 3 | 0031.3804
6 | D404,D604,D504 | SMB_Handsoldering | 3 | 60V
7 | D403,D503,D603,D302,D1402,D1302,D1202,D1102,D1002,D902,D802,D202,D702 | LED_1206 | 13 | GREEN
8 | R401,R501,R601 | R_1206_HandSoldering | 3 | 1.5k
9 | C304 | C_1206_HandSoldering | 1 | 47uF
10 | C302,C1403,C1303,C1203,C1103,C1003,C903,C803,C203 | R_0805_HandSoldering | 9 | 2.2uF
11 | R303 | R_1206_HandSoldering | 1 | 12k
12 | D301,D1401,D1301,D1201,D1101,D1001,D901,D801,D201 | SMA_Handsoldering | 9 | DIODESCH
13 | R302,R1402,R1302,R1202,R1102,R1002,R902,R802,R202 | R_1206_HandSoldering | 9 | 47.5k
14 | C301,C1401,C1402,C1302,C1301,C1201,C1202,C1102,C1101,C1002,C1001,C901,C902,C801,C802,C202,C201 | C_1210_HandSoldering | 17 | 2.2uF
15 | C303,C1404,C1304,C1204,C1104,C1004,C904,C804,C204 | R_1206_HandSoldering | 9 | 0.1uF
16 | R301,R1401,R1301,R1201,R1101,R1001,R901,R801,R201,R101,R102,R103,R104,R105,R107,R108,R109,R110,R111,R112,R113,R114,R106 | R_1206_HandSoldering | 23 | 0
17 | VR301 | BOURNS_MULTITURNPOT_3299W | 1 | 100k
18 | D303 | SMB_Handsoldering | 1 | 7.5V
19 | D1404,D1304,D1204,D1104,D1004,D904,D804,D204 | SMB_Handsoldering | 8 | 28V
20 | C1406,C1405,C1305,C1306,C1205,C1206,C1106,C1105,C1006,C1005,C906,C905,C806,C805,C205,C206 | C_1206_HandSoldering | 16 | 4.7uF
21 | R1403,R1303,R1203,R1103,R1003,R903,R803,R203 | R_1206_HandSoldering | 8 | 20k
22 | D1403,D1303,D1203,D1103,D1003,D903,D803,D203 | SMA_Handsoldering | 8 | 18V
23 | L1401,L1301,L1201,L1101,L1001,L901,L801,L201 | 47uIND_CDRH127_LDNP-470MC_SUMIDA | 8 | 47uH
24 | VR1401,VR1301,VR1201,VR1101,VR1001,VR901,VR801,VR201 | BOURNS_MULTITURNPOT_3299W | 8 | 1M
25 | R1404,R1304,R1204,R1104,R1004,R904,R804,R204 | R_1206_HandSoldering | 8 | 400
26 | C702 | SMD-1206_Pol | 1 | 10uF
27 | D701 | LED_1206 | 1 | RED
28 | R701 | SMD-1206_Pol | 1 | 100k
29 | R702,R703 | SMD-1206_Pol | 2 | 500k
30 | R704,R706 | SMD-1206_Pol | 2 | 10k
31 | R705,R709,R304 | SMD-1206_Pol | 3 | 300
32 | U701 | Reg_SOT89-3_Diodes_PinNames | 1 | UA78L05CPK
33 | J104,J110,J111,J112,J113,J114,J115,J116,J117,J118,J119,J120,J121,J122,J123,J124,J125,J126,J127,J128,J129 | CONN_PHOENIX_1844210_2PIN | 21 | CONN_01X02
34 | C701,C703 | C_1206_HandSoldering | 2 | C
35 | U703 | LT_LTC2950-1_TSOT-23-8 | 1 | LTC2950-1
36 | J105 | CONN_PHOENIX_1720466_2PIN | 1 | CONN_01X02
37 | R707,R708 | SMD-1206_Pol | 2 | 1M
38 | L301 | 15uIND_SLF10165T-150M3R13PF_BOURNS | 1 | 15uH
39 | SW701 | PBSW_CW_GPTS203211B | 1 | GPTS203211B
40 | J130,J131,J132,J133 | MountingHole_5.5mm_Pad_Via | 4 | MOUNTING_HOLE
41 | D401,D601,D501 | DD-PAK_TO263_SingleDiode_ThermalVias | 3 | VB30100S-E3/8W
42 | G*** | ParadigmLogo | 1 | LOGO
43 | D402,D502,D602 | SOD-123 | 3 | 25V
44 | U201,U301,U801,U901,U1001,U1101,U1201,U1301,U1401 | LMR16030S_8-PowerSOIC_TI | 9 | LMR16030S
45 | J101,J102,J103,J106,J108,J109 | CONN_PHOENIX_1844236_4PIN_1 | 6 | CONN_01X04
46 | G*** | ParadigmLogoRelief | 1 | LOGO

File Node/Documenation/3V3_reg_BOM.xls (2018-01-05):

Part | Manufacturer | Part Number | Quantity | Price | Attribute 1 Name | Attribute 1 Value | Attribute 2 Name | Attribute 2 Value | Attribute 3 Name | Attribute 3 Value | Footprint
Cin | TDK | C1005X6S1C105K050BC | 1 | 0.02 | Cap | 1uF | ESR | 0.011Ohm |  |  | 0402
Cout | MuRata | GRM188R60J105KA01D | 1 | 0.01 | Cap | 1uF | ESR | 6.065mOhm |  |  | 0603
U1 | Texas Instruments | TPS79501DRBR | 1 | 1 |  |  |  |  |  |  | DRB0008B
Cfb | Yageo America | CC0201JRNPO8BN150 | 1 | 0.01 | Cap | 15pF | ESR | 0Ohm |  |  | 0201
Rfbb | Vishay-Dale | CRCW040230K1FKED | 1 | 0.01 | Resistance | 30.1kOhm | Tolerance | 1% | Power | 0.063W | 0402
Rfbt | Yageo America | RC0603FR-0751KL | 1 | 0.01 | Resistance | 51kOhm | Tolerance | 1% | Power | 0.1W | 0603

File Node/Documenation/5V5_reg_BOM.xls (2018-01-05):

Part | Manufacturer | Part Number | Quantity | Price | Attribute 1 Name | Attribute 1 Value | Attribute 2 Name | Attribute 2 Value | Attribute 3 Name | Attribute 3 Value | Footprint
Cboot | MuRata | GRM155R61A104KA01D | 1 | 0.01 | Cap | 100nF | ESR | 0Ohm |  |  | 0402
Ccomp | MuRata | GRM033C80J123KE01D | 1 | 0.01 | Cap | 12nF | ESR | 0Ohm |  |  | 0201
Ccomp2 | MuRata | GRM1555C1H9R1CA01D | 1 | 0.01 | Cap | 9.1pF | ESR | 0Ohm |  |  | 0402
Cin | TDK | CGA4J3X7R1H225K125AB | 2 | 0.12 | Cap | 2.2uF | ESR | 3.288mOhm |  |  | 0805
Cout | Panasonic | 10TPE47MAZB | 1 | 0.38 | Cap | 47uF | ESR | 0.035Ohm |  |  | 3528-21
Css | Yageo America | CC0805KRX7R9BB272 | 1 | 0.01 | Cap | 2.7nF | ESR | 0Ohm |  |  | 0805
D1 | Diodes Inc. | B560C-13-F | 1 | 0.19 | VFatIo | 0.7V | Io | 5A | VRRM | 60V | SMC
L1 | Bourns | SDR0604-330KL | 1 | 0.19 | L | 33uH | DCR | 0.25Ohm | IDC | 0.88A | SDR0604
Rcomp | Vishay-Dale | CRCW040217K4FKED | 1 | 0.01 | Resistance | 17.4kOhm | Tolerance | 1% | Power | 0.063W | 0402
Rfbb | Vishay-Dale | CRCW040211K3FKED | 1 | 0.01 | Resistance | 11.3kOhm | Tolerance | 1% | Power | 0.063W | 0402
Rfbt | Panasonic | ERJ-6ENF6652V | 1 | 0.01 | Resistance | 66.5kOhm | Tolerance | 1% | Power | 0.125W | 0805
Rpg | Vishay-Dale | CRCW04021K05FKED | 1 | 0.01 | Resistance | 1.05kOhm | Tolerance | 1% | Power | 0.063W | 0402
Rt | Vishay-Dale | CRCW0402124KFKED | 1 | 0.01 | Resistance | 124kOhm | Tolerance | 1% | Power | 0.063W | 0402
U1 | Texas Instruments | TPS54361DPRR | 1 | 2 |  |  |  |  |  |  | DPR0010A

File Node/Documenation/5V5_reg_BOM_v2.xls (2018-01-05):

Part | Manufacturer | Part Number | Quantity | Price | Attribute 1 Name | Attribute 1 Value | Attribute 2 Name | Attribute 2 Value | Attribute 3 Name | Attribute 3 Value | Footprint
Cboot | MuRata | GRM155R61A104KA01D | 1 | 0.01 | Cap | 100nF | ESR | 1mOhm |  |  | 0402
Ccomp | Kemet | C0603C123J3GACTU | 1 | 0.09 | Cap | 12nF | ESR | 0Ohm |  |  | 0603
Ccomp2 | Kemet | C0805C100K5GACTU | 1 | 0.01 | Cap | 10pF | ESR | 0Ohm |  |  | 0805
Cin | TDK | C2012X7R1H225K125AC | 2 | 0.13 | Cap | 2.2uF | ESR | 3.66mOhm |  |  | 0805
Cout | Panasonic | 10TPE47MAZB | 1 | 0.38 | Cap | 47uF | ESR | 0.035Ohm |  |  | 3528-21
Css | MuRata | GRM1885C1H272JA01J | 1 | 0.01 | Cap | 2.7nF | ESR | 0Ohm |  |  | 0603
D1 | Diodes Inc. | B560C-13-F | 1 | 0.19 | VFatIo | 0.7V | Io | 5A | VRRM | 60V | SMC
L1 | Bourns | SRR6028-330Y | 1 | 0.27 | L | 33uH | DCR | 0.16Ohm | IDC | 0.92A | SRR6028
Rcomp | Vishay-Dale | CRCW040217K4FKED | 1 | 0.01 | Resistance | 17.4kOhm | Tolerance | 1% | Power | 0.063W | 0402
Rfbb | Panasonic | ERJ-6ENF1132V | 1 | 0.01 | Resistance | 11.3kOhm | Tolerance | 1% | Power | 0.125W | 0805
Rfbt | Vishay-Dale | CRCW040266K5FKED | 1 | 0.01 | Resistance | 66.5kOhm | Tolerance | 1% | Power | 0.063W | 0402
Rpg | Vishay-Dale | CRCW04021K02FKED | 1 | 0.01 | Resistance | 1.02kOhm | Tolerance | 1% | Power | 0.063W | 0402
Rt | Vishay-Dale | CRCW0402124KFKED | 1 | 0.01 | Resistance | 124kOhm | Tolerance | 1% | Power | 0.063W | 0402
U1 | Texas Instruments | TPS54361DPRR | 1 | 2 |  |  |  |  |  |  | DPR0010A

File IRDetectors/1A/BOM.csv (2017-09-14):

Component | Description | Part | References | Value | Footprint | Quantity Per PCB | Datasheet | Supporting
1 | Unpolarized capacitor | C | C6 C7 C9 C12 C15 C16 | 100n | C_0603_HandSoldering | 6 | https://www.digikey.com/product-detail/en/murata-electronics-north-america/GRM31CR60J107KE39L/490-13982-1-ND/6155812 | https://www.digikey.com/product-detail/en/murata-electronics-north-america/GRM31CR60J107KE39L/490-13982-1-ND/6155812
2 | Unpolarized capacitor | C | C1 C2 | 10n | C_0603_HandSoldering | 2 | https://www.digikey.com/product-detail/en/murata-electronics-north-america/GRM31CR60J107KE39L/490-13982-1-ND/6155812 | https://www.digikey.com/product-detail/en/murata-electronics-north-america/GRM31CR60J107KE39L/490-13982-1-ND/6155812
3 | Unpolarized capacitor | C | C13 C14 | 10u | C_0805_HandSoldering | 2 | https://www.digikey.com/product-detail/en/murata-electronics-north-america/GRM188R60J106KE47D/490-12538-1-ND/5797528 | https://www.digikey.com/product-detail/en/murata-electronics-north-america/GRM188R60J106KE47D/490-12538-1-ND/5797528
4 | Unpolarized capacitor | C | C8 C10 | 1u | C_0603_HandSoldering | 2 | https://www.digikey.com/product-detail/en/samsung-electro-mechanics-america-inc/CL10A105KQ8NNNC/1276-1036-1-ND/3889122 | https://www.digikey.com/product-detail/en/samsung-electro-mechanics-america-inc/CL10A105KQ8NNNC/1276-1036-1-ND/3889122
5 | Unpolarized capacitor | C | C4 C5 | 22p | C_0603_HandSoldering | 2 | https://www.digikey.com/product-detail/en/samsung-electro-mechanics-america-inc/CL10C220JB8NFNC/1276-2228-1-ND/3890314 | https://www.digikey.com/product-detail/en/samsung-electro-mechanics-america-inc/CL10C220JB8NFNC/1276-2228-1-ND/3890314
6 | Polarised capacitor | CP | C11 | 22u | C_0805_HandSoldering | 1 | https://www.digikey.com/product-detail/en/avx-corporation/F920J226MPA/478-8119-1-ND/4005716 | https://www.digikey.com/product-detail/en/avx-corporation/F920J226MPA/478-8119-1-ND/4005716
7 | Unpolarized capacitor | C | C3 | 22u | C_0805_HandSoldering | 1 | https://www.digikey.com/product-detail/en/samsung-electro-mechanics-america-inc/CL21A226KQCLRNC/1276-6687-1-ND/5961546 | https://www.digikey.com/product-detail/en/samsung-electro-mechanics-america-inc/CL21A226KQCLRNC/1276-6687-1-ND/5961546
8 | LED generic | LED | D1 | D0_ACT | LED_0603 | 1 | https://www.digikey.com/product-detail/en/wurth-electronics-inc/150060BS75000/732-4966-1-ND/4489893 | https://www.digikey.com/product-detail/en/wurth-electronics-inc/150060BS75000/732-4966-1-ND/4489893
9 | LED generic | LED | D4 | D1_ACT | LED_0603 | 1 | https://www.digikey.com/product-detail/en/wurth-electronics-inc/150060BS75000/732-4966-1-ND/4489893 | https://www.digikey.com/product-detail/en/wurth-electronics-inc/150060BS75000/732-4966-1-ND/4489893
10 | Diode | D | D11 | D_RST | D_0603 | 1 | https://www.digikey.com/product-detail/en/avx-corporation/SD0805S040S0R5/478-7802-1-ND/3749494 | https://www.digikey.com/product-detail/en/avx-corporation/SD0805S040S0R5/478-7802-1-ND/3749494
11 | Diode | D | D9 | D_VCOM | D_0603 | 1 | https://www.digikey.com/product-detail/en/avx-corporation/SD0805S040S0R5/478-7802-1-ND/3749494 | https://www.digikey.com/product-detail/en/avx-corporation/SD0805S040S0R5/478-7802-1-ND/3749494
12 | LED generic | LED | D5 | LED0 | LED_0603 | 1 | https://www.digikey.com/product-detail/en/wurth-electronics-inc/150060BS75000/732-4966-1-ND/4489893 | https://www.digikey.com/product-detail/en/wurth-electronics-inc/150060BS75000/732-4966-1-ND/4489893
13 | LED generic | LED | D6 | LED1 | LED_0603 | 1 | https://www.digikey.com/product-detail/en/wurth-electronics-inc/150060BS75000/732-4966-1-ND/4489894 | https://www.digikey.com/product-detail/en/wurth-electronics-inc/150060BS75000/732-4966-1-ND/4489894
14 | LED generic | LED | D7 | LED2 | LED_0603 | 1 | https://www.digikey.com/product-detail/en/wurth-electronics-inc/150060BS75000/732-4966-1-ND/4489895 | https://www.digikey.com/product-detail/en/wurth-electronics-inc/150060BS75000/732-4966-1-ND/4489895
15 | LED generic | LED | D8 | LED3 | LED_0603 | 1 | https://www.digikey.com/product-detail/en/wurth-electronics-inc/150060BS75000/732-4966-1-ND/4489896 | https://www.digikey.com/product-detail/en/wurth-electronics-inc/150060BS75000/732-4966-1-ND/4489896
16 | LED generic | LED | D12 | PWR_LED | LED_0603 | 1 | https://www.digikey.com/product-detail/en/wurth-electronics-inc/150060BS75000/732-4966-1-ND/4489897 | https://www.digikey.com/product-detail/en/wurth-electronics-inc/150060BS75000/732-4966-1-ND/4489897
17 | LED generic | LED | D13 | RX_LED | LED_0603 | 1 | https://www.digikey.com/product-detail/en/wurth-electronics-inc/150060BS75000/732-4966-1-ND/4489898 | https://www.digikey.com/product-detail/en/wurth-electronics-inc/150060BS75000/732-4966-1-ND/4489898
18 | LED generic | LED | D3 | SCL | LED_0603 | 1 | https://www.digikey.com/product-detail/en/wurth-electronics-inc/150060BS75000/732-4966-1-ND/4489899 | https://www.digikey.com/product-detail/en/wurth-electronics-inc/150060BS75000/732-4966-1-ND/4489899
19 | LED generic | LED | D2 | SDA | LED_0603 | 1 | https://www.digikey.com/product-detail/en/wurth-electronics-inc/150060BS75000/732-4966-1-ND/4489900 | https://www.digikey.com/product-detail/en/wurth-electronics-inc/150060BS75000/732-4966-1-ND/4489900
20 | LED generic | LED | D14 | TX_LED | LED_0603 | 1 | https://www.digikey.com/product-detail/en/wurth-electronics-inc/150060BS75000/732-4966-1-ND/4489901 | https://www.digikey.com/product-detail/en/wurth-electronics-inc/150060BS75000/732-4966-1-ND/4489901
21 | LED generic | LED | D10 | VCOM_PWR | LED_0603 | 1 | https://www.digikey.com/product-detail/en/wurth-electronics-inc/150060BS75000/732-4966-1-ND/4489902 | https://www.digikey.com/product-detail/en/wurth-electronics-inc/150060BS75000/732-4966-1-ND/4489902
22 | Fuse, generic | Fuse | F500 | 500mA | R_1812_HandSoldering | 1 | https://www.digikey.com/product-detail/en/bourns-inc/MF-MSMF050-2/MF-MSMF050-2CT-ND/662842 | https://www.digikey.com/product-detail/en/bourns-inc/MF-MSMF050-2/MF-MSMF050-2CT-ND/662842
23 | Trim-Potentionmeter | POT_TRIM | FREQ1 | POT_TRIM | Potentiometer_Trimmer_Vishay_T73XW_Vertical | 1 | https://www.digikey.com/product-detail/en/vishay-spectrol/M64W501KB40/SP064W-500-ND/1287456 | https://www.digikey.com/product-detail/en/vishay-spectrol/M64W501KB40/SP064W-500-ND/1287456
24 | RJ45, status leds | RJ45_LEDS | J1 J2 | RJ45_LEDS | RJ45_8P8C_90DEG_LEDs | 2 | https://www.digikey.com/product-detail/en/amphenol-commercial-products/RJE73-188-00140/RJE73-188-00140CT-ND/3727131 | https://www.digikey.com/product-detail/en/amphenol-commercial-products/RJE73-188-00140/RJE73-188-00140CT-ND/3727131
25 | Dual Jumper, normally closed | Jumper_NC_Dual | JP3 | Emitter Current Source | Pin_Header_Straight_1x03_Pitch2.54mm | 1 | https://www.digikey.com/product-detail/en/amphenol-fci/68000-200HLF/609-5099-1-ND/5968545 | https://www.digikey.com/product-detail/en/amphenol-fci/68000-200HLF/609-5099-1-ND/5968545
26 | Jumper, normally closed | Jumper_NC_Small | JP2 | GND_EN | Pin_Header_Straight_1x02_Pitch2.54mm | 1 | https://www.digikey.com/product-detail/en/amphenol-fci/67996-200HLF/609-5098-1-ND/5968543 | https://www.digikey.com/product-detail/en/amphenol-fci/67996-200HLF/609-5098-1-ND/5968543
27 | Dual Jumper, normally closed | Jumper_NC_Dual | JP4 | IR_SYNC_SELECT | Pin_Header_Straight_1x03_Pitch2.54mm | 1
28 | Jumper, normally closed | Jumper_NC_Small | JP1 | VCOM_EN | Pin_Header_Straight_1x02_Pitch2.54mm | 1
29 | Ferrite bead | Ferrite_Bead | MH2029-300Y1 | Ferrite_Bead | R_0805 | 1 | https://www.digikey.com/product-detail/en/bourns-inc/MH2029-300Y/MH2029-300YCT-ND/3741761 | https://www.digikey.com/product-detail/en/bourns-inc/MH2029-300Y/MH2029-300YCT-ND/3741761
30 | Connector, single row, 01x08 | CONN_01X08 | P4 | CONN_01X08 | Pin_Header_Straight_1x08_Pitch2.54mm | 1
31 | Connector, single row, 01x02 | CONN_01X02 | P6 | CONN_IR0 | Pin_Header_Straight_1x02_Pitch2.54mm | 1
32 | Connector, single row, 01x02 | CONN_01X02 | P5 | CONN_IR1 | Pin_Header_Straight_1x02_Pitch2.54mm | 1
33 | Connector, single row, 01x03 | CONN_01X03 | P2 | CONN_PD0 | Pin_Header_Straight_1x03_Pitch2.54mm | 1
34 | Connector, single row, 01x03 | CONN_01X03 | P1 | CONN_PD1 | Pin_Header_Straight_1x03_Pitch2.54mm | 1
35 | Connector, single row, 01x03 | CONN_01X03 | P3 | I2C _CONN | PhoenixContact_MC-G_03x3.50mm_Angled | 1 | https://www.digikey.com/product-detail/en/molex-llc/0395021003/WM7771-ND/1280622 | https://www.digikey.com/product-detail/en/molex-llc/0395021003/WM7771-ND/1280622 | https://www.digikey.com/product-detail/en/molex-llc/0395000003/WM7733-ND/1280584
36 | Connector, double row, 02x03 | CONN_02X03 | P10 | ISP | Socket_Strip_Straight_2x03_Pitch2.54mm | 1
37 | Connector, single row, 01x02 | CONN_01X02 | P7 | PWR_IN | PhoenixContact_MC-G_02x3.50mm_Angled | 1 | https://www.digikey.com/product-detail/en/molex-llc/0395021002/WM7770-ND/1280621 | https://www.digikey.com/product-detail/en/molex-llc/0395021002/WM7770-ND/1280621 | https://www.digikey.com/product-detail/en/molex-llc/39500-0002/WM7732-ND/1280583
38 | Connector, single row, 01x04 | CONN_01X04 | P8 | RS485_CONN | PhoenixContact_MC-G_04x3.50mm_Angled | 1 | https://www.digikey.com/product-detail/en/molex-llc/0395021004/WM7772-ND/1280623 | https://www.digikey.com/product-detail/en/molex-llc/0395021004/WM7772-ND/1280623 | https://www.digikey.com/product-detail/en/molex-llc/39500-0004/WM7734-ND/1280585
39 | USB micro/mini connector | USB_OTG | P9 | USB_MICRO | USB_Micro-B | 1 | https://www.digikey.com/product-detail/en/amphenol-fci/10118192-0001LF/609-4613-1-ND/2785378 | https://www.digikey.com/product-detail/en/amphenol-fci/10118192-0001LF/609-4613-1-ND/2785378
40 | Transistor P-MOSFET with substrate diode (general) | Q_PMOS_SDG | Q3 | FDN340PCT | SC-59 | 1 | https://www.digikey.com/product-detail/en/fairchild-on-semiconductor/FDN340P/FDN340PCT-ND/965604 | https://www.digikey.com/product-detail/en/fairchild-on-semiconductor/FDN340P/FDN340PCT-ND/965604
41 | Transistor N-JFET (general) | Q_NJFET_DGS | Q1 Q2 | FDN340PCT-ND | SC-59 | 2 | https://www.digikey.com/product-detail/en/fairchild-on-semiconductor/FDN340P/FDN340PCT-ND/965604 | https://www.digikey.com/product-detail/en/fairchild-on-semiconductor/FDN340P/FDN340PCT-ND/965604
42 | Transistor P-MOSFET with substrate diode (general) | Q_PMOS_SDG | Q4 | FDN340PCT-ND | SC-59 | 1 | https://www.digikey.com/product-detail/en/fairchild-on-semiconductor/FDN340P/FDN340PCT-ND/965604 | https://www.digikey.com/product-detail/en/fairchild-on-semiconductor/FDN340P/FDN340PCT-ND/965604
43 | Resistor | R | R1 R2 R3 R4 R16 R21 R23 R26 R32 R33 R36 R46 R48 | 0 | R_0603_HandSoldering | 13 | https://www.digikey.com/product-detail/en/yageo/RC0603JR-070RL/311-0.0GRCT-ND/729622 | https://www.digikey.com/product-detail/en/yageo/RC0603JR-070RL/311-0.0GRCT-ND/729622
44 | Resistor | R | R35 | 100k | R_0603_HandSoldering | 1 | https://www.digikey.com/product-detail/en/yageo/RC0603JR-07100KL/311-100KGRCT-ND/729645 | https://www.digikey.com/product-detail/en/yageo/RC0603JR-07100KL/311-100KGRCT-ND/729645
45 | Resistor | R | R37 R38 R39 R42 R43 | 10k | R_0603_HandSoldering | 5 | https://www.digikey.com/product-detail/en/yageo/RC0603JR-0710KL/311-10KGRCT-ND/729647 | https://www.digikey.com/product-detail/en/yageo/RC0603JR-0710KL/311-10KGRCT-ND/729647
46 | Resistor | R | R24 R25 | 120 | R_0603_HandSoldering | 2 | https://www.digikey.com/product-detail/en/yageo/RC0603JR-07120RL/311-120GRCT-ND/729653 | https://www.digikey.com/product-detail/en/yageo/RC0603JR-07120RL/311-120GRCT-ND/729653
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

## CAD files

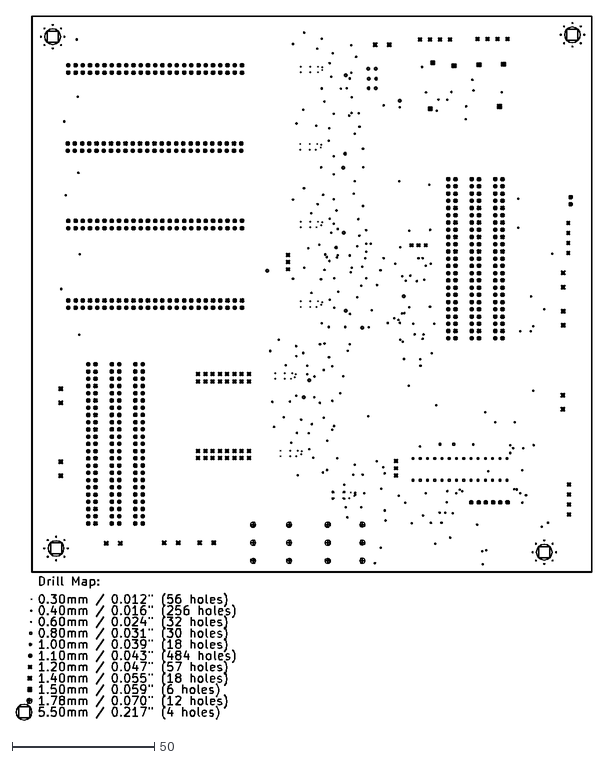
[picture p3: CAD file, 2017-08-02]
Motherboard/Motherboard_REV2-1_TempoAuto_8_2_2017/Motherboard_8_2_2017_GERB/Motherboard-drl_map.dxf
202.0 x 247.1

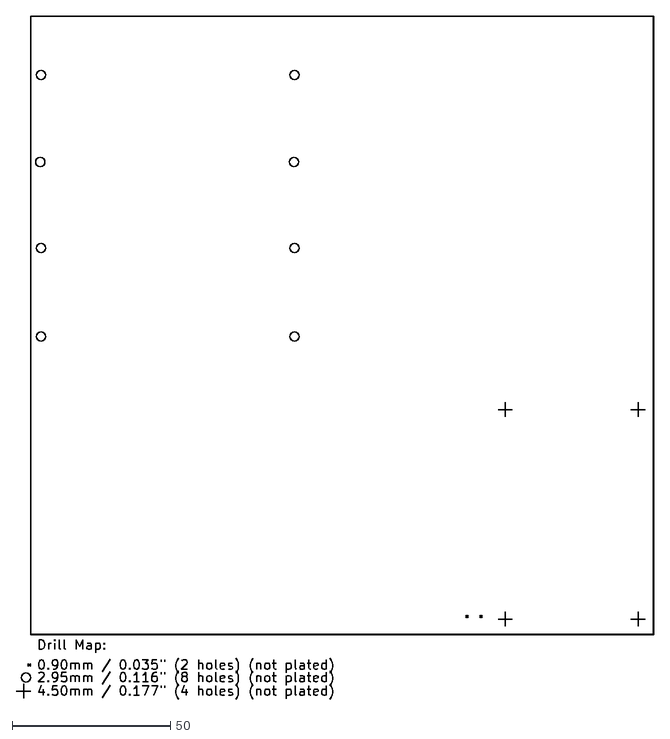
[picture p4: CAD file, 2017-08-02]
Motherboard/Motherboard_REV2-1_TempoAuto_8_2_2017/Motherboard_8_2_2017_GERB/Motherboard-NPTH-drl_map.dxf
201.0 x 215.5

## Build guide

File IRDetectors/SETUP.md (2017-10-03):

# Flashing the IRDetectors

Flashing a bootloader onto an AVR microprocessor can be done many ways. In this tutorial, we will 
flash the Arduino Bootloader onto the AVR using the arduino IDE.  You can also flash your own firmware
using the AVR C toolchain and `avrdude`.  I'll go into that at the bottom under "Custom Firmware".

If this tutorial isn't working for you, there are tons of other resources out there to help you

## Arduino As ISP

I flash my AVRs with an Arduino Micro as my programmer.

> **What is a programmer?** A programmer is just a peice of hardware with an SPI controller and some 
> GPIO and power pins. An arduino is a generic microcontroller that can be used to flash other 
> microcontrollers with bootloaders from your laptop.  TL;DR: Your laptop doesn't have a SPI interface, to 
> flash a bootloader you need an SPI interface, an arduino has a SPI interface

This is fairly easy to do with a working Arduino. 

1. Attach your arduino to your computer over USB
2. Open the Arduino IDE > File > Examples > 10. Arduino ISP > Arduino ISP
3. Select Port: Tools > Port > Select the port connected to the Arduino (Unplug check which one disappeared)
4. Select Board: Tools > Board > Arduino/Genuino Micro
5. Click the upload button in the IDE (or Sketch > Upload)

You should see some LEDs on the Arduino flash and a message on the bottom of the IDE that says "Done Uploading!"

## Wiring

The ISP Connection on the IR Detector board has the following pinout (orient with RJ45 Jacks on the bottom)

1. Top Left: VCC (5V)
2. Top Right: MISO
3. Mid Left: MOSI
4. Mid Right: SCK
5. Bottom Left: GND
6. Bottom Right: RESET

You should connect these with jumpers to the arduino. Connect RESET to digital pin 10 on the arduino. 
All other pins on the ISP connection should go to the like named pin on the Arduino (i.e. MOSI on the arduino -> MOSI on ISP)

## Flashing Bootloader

Back in the Arduino IDE, 
1. Go to Preferences (on mac: CMD + ,) and check the boxes for Verbose Output during Compilation and Upload
2. Go to Tools > Programmer > Arduino as ISP
3. Burn: Tools > Burn Bootloader

You should see the following output

```
Applications/Arduino.app/Contents/Java/hardware/tools/avr/bin/avrdude -C/Applications/Arduino.app/Contents/Java/hardware/tools/avr/etc/avrdude.conf -v -patmega32u4 -cstk500v1 -P/dev/cu.usbmodem14411 -b19200 -e -Ulock:w:0x3F:m -Uefuse:w:0xcb:m -Uhfuse:w:0xd8:m -Ulfuse:w:0xff:m 

avrdude: Version 6.3, compiled on Dec 16 2016 at 13:32:25
         Copyright (c) 2000-2005 Brian Dean, http://www.bdmicro.com/
         Copyright (c) 2007-2014 Joerg Wunsch

         System wide configuration file is "/Applications/Arduino.app/Contents/Java/hardware/tools/avr/etc/avrdude.conf"
         User configuration file is "/Users/edhurtig/.avrduderc"
         User configuration file does not exist or is not a regular file, skipping

         Using Port                    : /dev/cu.usbmodem14411
         Using Programmer              : stk500v1
         Overriding Baud Rate          : 19200
         AVR Part                      : ATmega32U4
         Chip Erase delay              : 9000 us
         PAGEL                         : PD7
         BS2                           : PA0
         RESET disposition             : dedicated
         RETRY pulse                   : SCK
         serial program mode           : yes
         parallel program mode         : yes
         Timeout                       : 200
         StabDelay                     : 100
         CmdexeDelay                   : 25
         SyncLoops                     : 32
         ByteDelay                     : 0
         PollIndex                     : 3
         PollValue                     : 0x53
         Memory Detail                 :

                                  Block Poll               Page                       Polled
           Memory Type Mode Delay Size  Indx Paged  Size   Size #Pages MinW  MaxW   ReadBack
           ----------- ---- ----- ----- ---- ------ ------ ---- ------ ----- ----- ---------
           eeprom        65    20     4    0 no       1024    4      0  9000  9000 0x00 0x00
           flash         65     6   128    0 yes     32768  128    256  4500  4500 0x00 0x00
           lfuse          0     0     0    0 no          1    0      0  9000  9000 0x00 0x00
           hfuse          0     0     0    0 no          1    0      0  9000  9000 0x00 0x00
           efuse          0     0     0    0 no          1    0      0  9000  9000 0x00 0x00
           lock           0     0     0    0 no          1    0      0  9000  9000 0x00 0x00
           calibration    0     0     0    0 no          1    0      0     0     0 0x00 0x00
           signature      0     0     0    0 no          3    0      0     0     0 0x00 0x00

         Programmer Type : STK500
         Description     : Atmel STK500 Version 1.x firmware
         Hardware Version: 2
         Firmware Version: 1.18
         Topcard         : Unknown
         Vtarget         : 0.0 V
         Varef           : 0.0 V
         Oscillator      : Off
         SCK period      : 0.1 us

avrdude: AVR device initialized and ready to accept instructions

/Applications/Arduino.app/Contents/Java/hardware/tools/avr/bin/avrdude -C/Applications/Arduino.app/Contents/Java/hardware/tools/avr/etc/avrdude.conf -v -patmega32u4 -cstk500v1 -P/dev/cu.usbmodem14411 -b19200 -Uflash:w:/Applications/Arduino.app/Contents/Java/hardware/arduino/avr/bootloaders/caterina/Caterina-Micro.hex:i -Ulock:w:0x2F:m 

avrdude: Version 6.3, compiled on Dec 16 2016 at 13:32:25
         Copyright (c) 2000-2005 Brian Dean, http://www.bdmicro.com/
         Copyright (c) 2007-2014 Joerg Wunsch

         System wide configuration file is "/Applications/Arduino.app/Contents/Java/hardware/tools/avr/etc/avrdude.conf"
         User configuration file is "/Users/edhurtig/.avrduderc"
         User configuration file does not exist or is not a regular file, skipping

         Using Port                    : /dev/cu.usbmodem14411
         Using Programmer              : stk500v1
         Overriding Baud Rate          : 19200
Reading | ################################################## | 100% 0.00s

avrdude: Device signature = 0x1e9587 (probably m32u4)
avrdude: erasing chip
avrdude: reading input file "0x3F"
avrdude: writing lock (1 bytes):

Writing | ################################################## | 100% 0.00s

avrdude: 1 bytes of lock written
avrdude: verifying lock memory against 0x3F:
avrdude: load data lock data from input file 0x3F:
avrdude: input file 0x3F contains 1 bytes
avrdude: reading on-chip lock data:

Reading | ################################################## | 100% 0.00s

avrdude: verifying ...
avrdude: 1 bytes of lock verified
avrdude: reading input file "0xcb"
avrdude: writing efuse (1 bytes):

Writing | ################################################## | 100% 0.00s

avrdude: 1 bytes of efuse written
avrdude: verifying efuse memory against 0xcb:
avrdude: load data efuse data from input file 0xcb:
avrdude: input file 0xcb contains 1 bytes
avrdude: reading on-chip efuse data:

Reading | ################################################## | 100% 0.00s

avrdude: verifying ...
avrdude: 1 bytes of efuse verified
avrdude: reading input file "0xd8"
avrdude: writing hfuse (1 bytes):

Writing | ################################################## | 100% 0.00s

avrdude: 1 bytes of hfuse written
avrdude: verifying hfuse memory against 0xd8:
avrdude: load data hfuse data from input file 0xd8:
avrdude: input file 0xd8 contains 1 bytes
avrdude: reading on-chip hfuse data:

Reading | ################################################## | 100% 0.00s

avrdude: verifying ...
avrdude: 1 bytes of hfuse verified
avrdude: reading input file "0xff"
avrdude: writing lfuse (1 bytes):

Writing | ################################################## | 100% 0.00s

avrdude: 1 bytes of lfuse written
avrdude: verifying lfuse memory against 0xff:
avrdude: load data lfuse data from input file 0xff:
avrdude: input file 0xff contains 1 bytes
avrdude: reading on-chip lfuse data:

Reading | ################################################## | 100% 0.00s

avrdude: verifying ...
avrdude: 1 bytes of lfuse verified

avrdude done.  Thank you.

         AVR Part                      : ATmega32U4
         Chip Erase delay              : 9000 us
         PAGEL                         : PD7
         BS2                           : PA0
         RESET disposition             : dedicated
         RETRY pulse                   : SCK
         serial program mode           : yes
         parallel program mode         : yes
         Timeout                       : 200
         StabDelay                     : 100
         CmdexeDelay                   : 25
         SyncLoops                     : 32
         ByteDelay                     : 0
         PollIndex                     : 3
         PollValue                     : 0x53
         Memory Detail                 :

                                  Block Poll               Page                       Polled
           Memory Type Mode Delay Size  Indx Paged  Size   Size #Pages MinW  MaxW   ReadBack
           ----------- ---- ----- ----- ---- ------ ------ ---- ------ ----- ----- ---------
           eeprom        65    20     4    0 no       1024    4      0  9000  9000 0x00 0x00
           flash         65     6   128    0 yes     32768  128    256  4500  4500 0x00 0x00
           lfuse          0     0     0    0 no          1    0      0  9000  9000 0x00 0x00
           hfuse          0     0     0    0 no          1    0      0  9000  9000 0x00 0x00
           efuse          0     0     0    0 no          1    0      0  9000  9000 0x00 0x00
           lock           0     0     0    0 no          1    0      0  9000  9000 0x00 0x00
           calibration    0     0     0    0 no          1    0      0     0     0 0x00 0x00
           signature      0     0     0    0 no          3    0      0     0     0 0x00 0x00

         Programmer Type : STK500
         Description     : Atmel STK500 Version 1.x firmware
         Hardware Version: 2
         Firmware Version: 1.18
         Topcard         : Unknown
         Vtarget         : 0.0 V
         Varef           : 0.0 V
         Oscillator      : Off
         SCK period      : 0.1 us

avrdude: AVR device initialized and ready to accept instructions

Reading | ################################################## | 100% 0.00s

avrdude: Device signature = 0x1e9587 (probably m32u4)
avrdude: NOTE: "flash" memory has been specified, an erase cycle will be performed
         To disable this feature, specify the -D option.
avrdude: erasing chip
avrdude: reading input file "/Applications/Arduino.app/Contents/Java/hardware/arduino/avr/bootloaders/caterina/Caterina-Micro.hex"
avrdude: writing flash (32730 bytes):

Writing | ################################################## | 100% 17.15s

avrdude: 32730 bytes of flash written
avrdude: verifying flash memory against /Applications/Arduino.app/Contents/Java/hardware/arduino/avr/bootloaders/caterina/Caterina-Micro.hex:
avrdude: load data flash data from input file /Applications/Arduino.app/Contents/Java/hardware/arduino/avr/bootloaders/caterina/Caterina-Micro.hex:
avrdude: input file /Applications/Arduino.app/Contents/Java/hardware/arduino/avr/bootloaders/caterina/Caterina-Micro.hex contains 32730 bytes
avrdude: reading on-chip flash data:

Reading | ################################################## | 100% 9.47s

avrdude: verifying ...
avrdude: 32730 bytes of flash verified
avrdude: reading input file "0x2F"
avrdude: writing lock (1 bytes):

Writing | ################################################## | 100% 0.01s

avrdude: 1 bytes of lock written
avrdude: verifying lock memory against 0x2F:
avrdude: load data lock data from input file 0x2F:
avrdude: input file 0x2F contains 1 bytes
avrdude: reading on-chip lock data:

Reading | ################################################## | 100% 0.00s

avrdude: verifying ...
avrdude: 1 bytes of lock verified

avrdude done.  Thank you.
```

## Custom Firmware

The following source code flashes the 4 debug LEDs on the IRDetector v1.1 board

```
#include <avr/io.h>
#include <util/delay.h>

int main(void)
{
  
    DDRB = 7 << 4;           /* make the LEDs on port B outputs */
    DDRE = 1 << 6;           /* make the LED on port E an output */

    /* insert your hardware initialization here */
    for(;;){
        char i;
        for(i = 0; i < 10; i++){
            _delay_ms(100);  /* max is 262.14 ms / F_CPU in MHz */
        }
        PORTB ^= 7 << 4;    /* toggle the LEDs on Port B */
        PORTE ^= 1 << 6;    /* toggle the LED on Port E*/
    }
    return 0;   /* never reached */
}
```

Save that as `main.c` then run the following in the same folder as main.c in a terminal window

```
avr-gcc -Wall -Os -DF_CPU=8000000 -mmcu=atmega32u4 -c main.c -o main.o
avr-gcc -Wall -Os -DF_CPU=8000000 -mmcu=atmega32u4 -o main.elf main.o
rm -f main.hex
avr-objcopy -j .text -j .data -O ihex main.elf main.hex
avr-size --format=avr --mcu=atmega32u4 main.elf
```

Then run the following to flash the AVR with the Arduino micro described above

```
avrdude -v -patmega32u4 -cstk500v1 -P/dev/cu.usbmodem14411  -p atmega32u4 -U flash:w:main.hex:i
```

**Note: Change /dev/cu.usbmodem14411 to the path to your arduino (see the Arduino IDE > Tools > Port)**

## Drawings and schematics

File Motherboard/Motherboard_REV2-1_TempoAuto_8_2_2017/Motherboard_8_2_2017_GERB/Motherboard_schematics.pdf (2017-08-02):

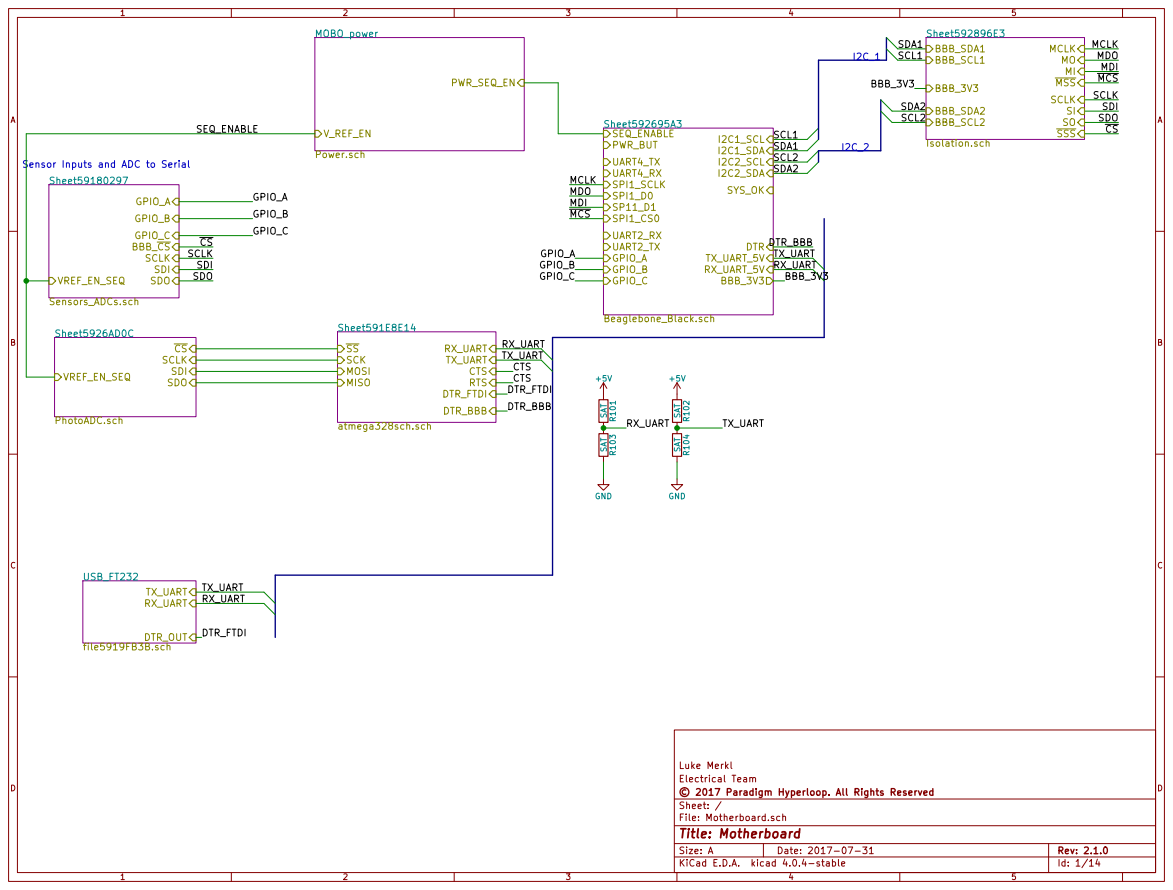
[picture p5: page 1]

Sensor Inputs and ADC to Serial
Sheet59180297

Luke Merkl
File: Motherboard.sch Sheet: / © 2017 Paradigm Hyperloop. All Rights Reserved Electrical Team

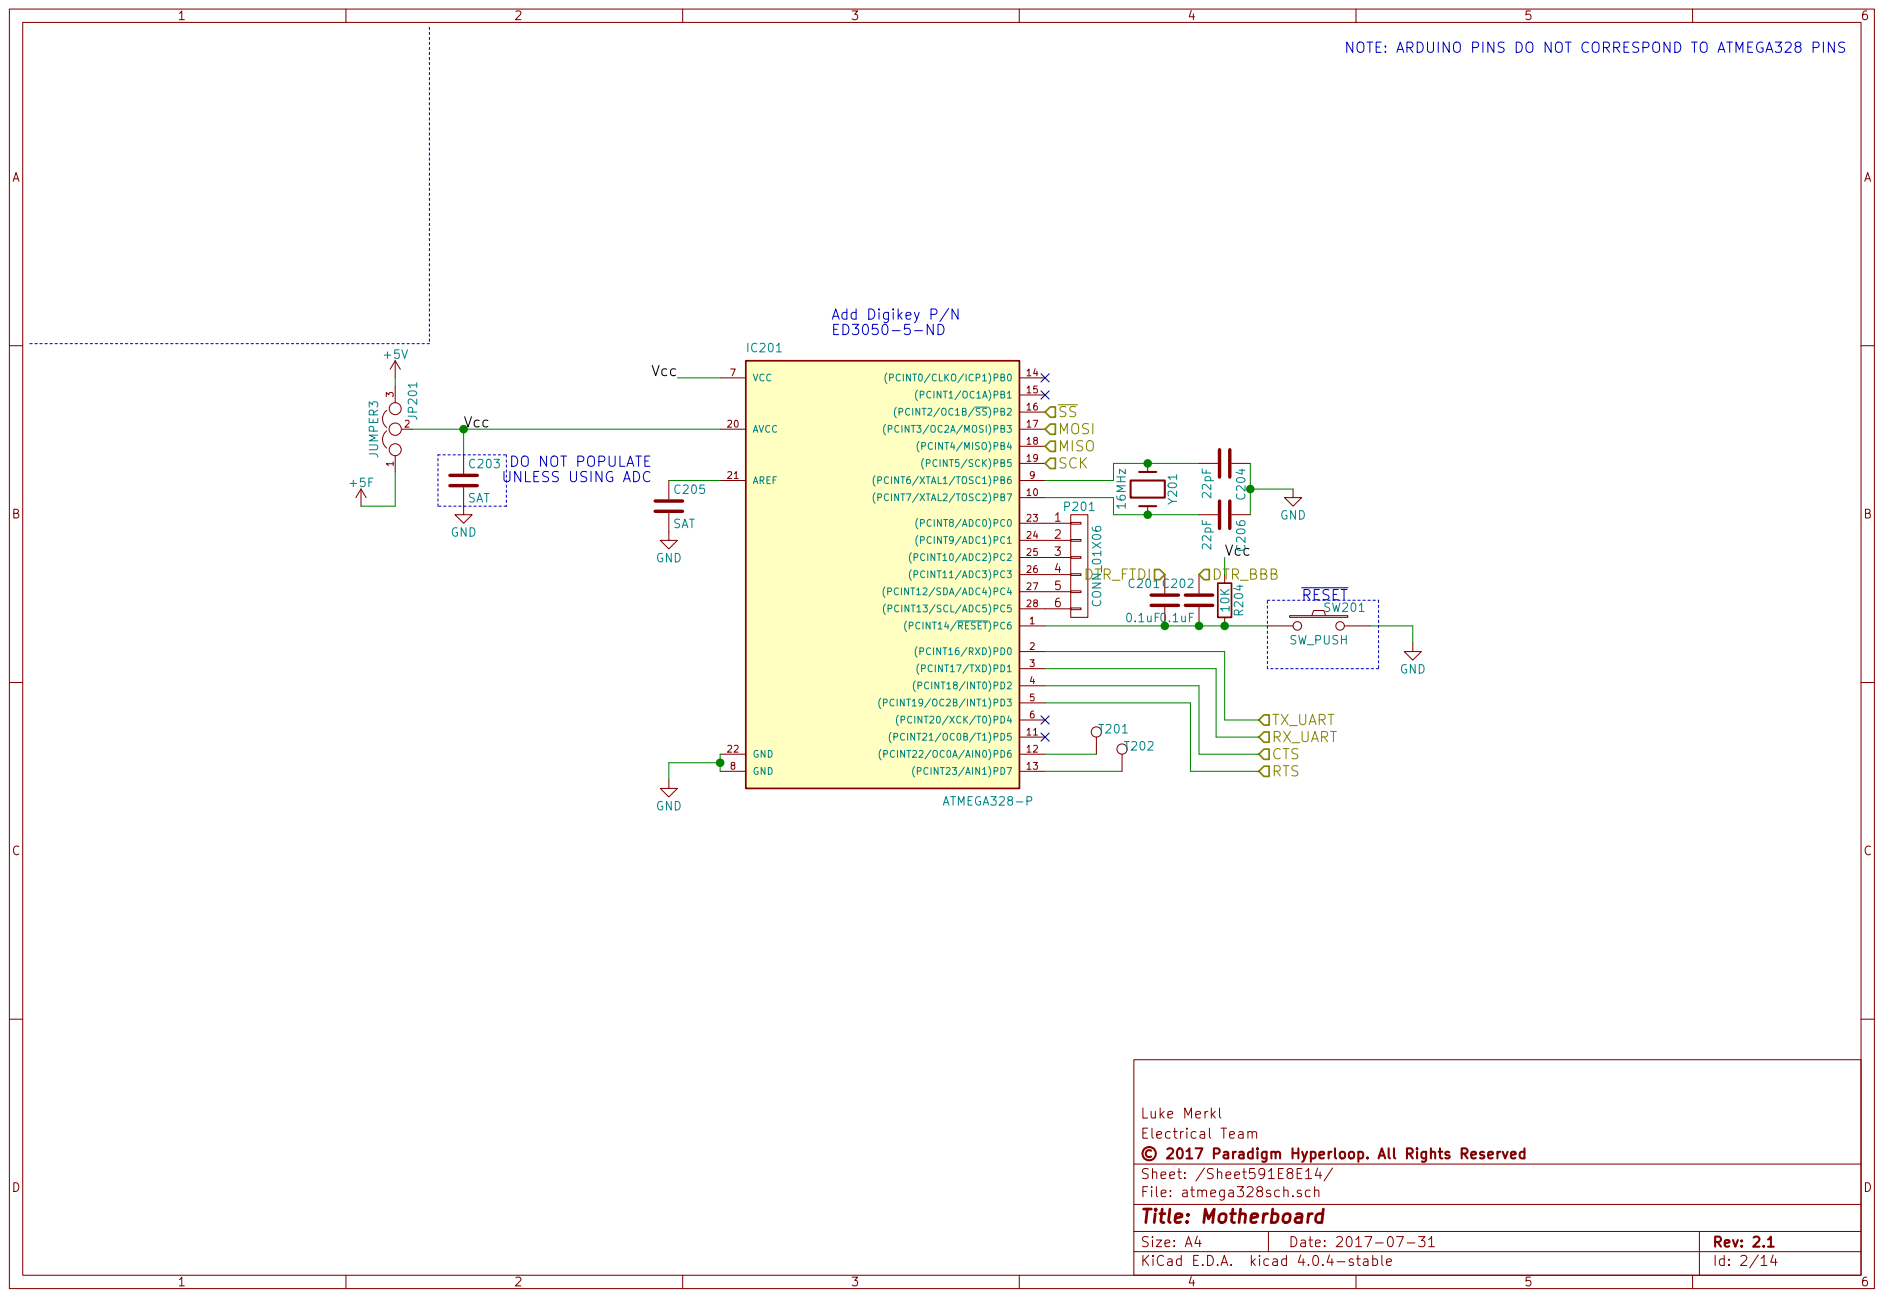
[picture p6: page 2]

NOTE: ARDUINO PINS DO NOT CORRESPOND TO ATMEGA328 PINS

Luke Merkl
File: atmega328sch.sch Sheet: /Sheet591E8E14/ © 2017 Paradigm Hyperloop. All Rights Reserved Electrical Team

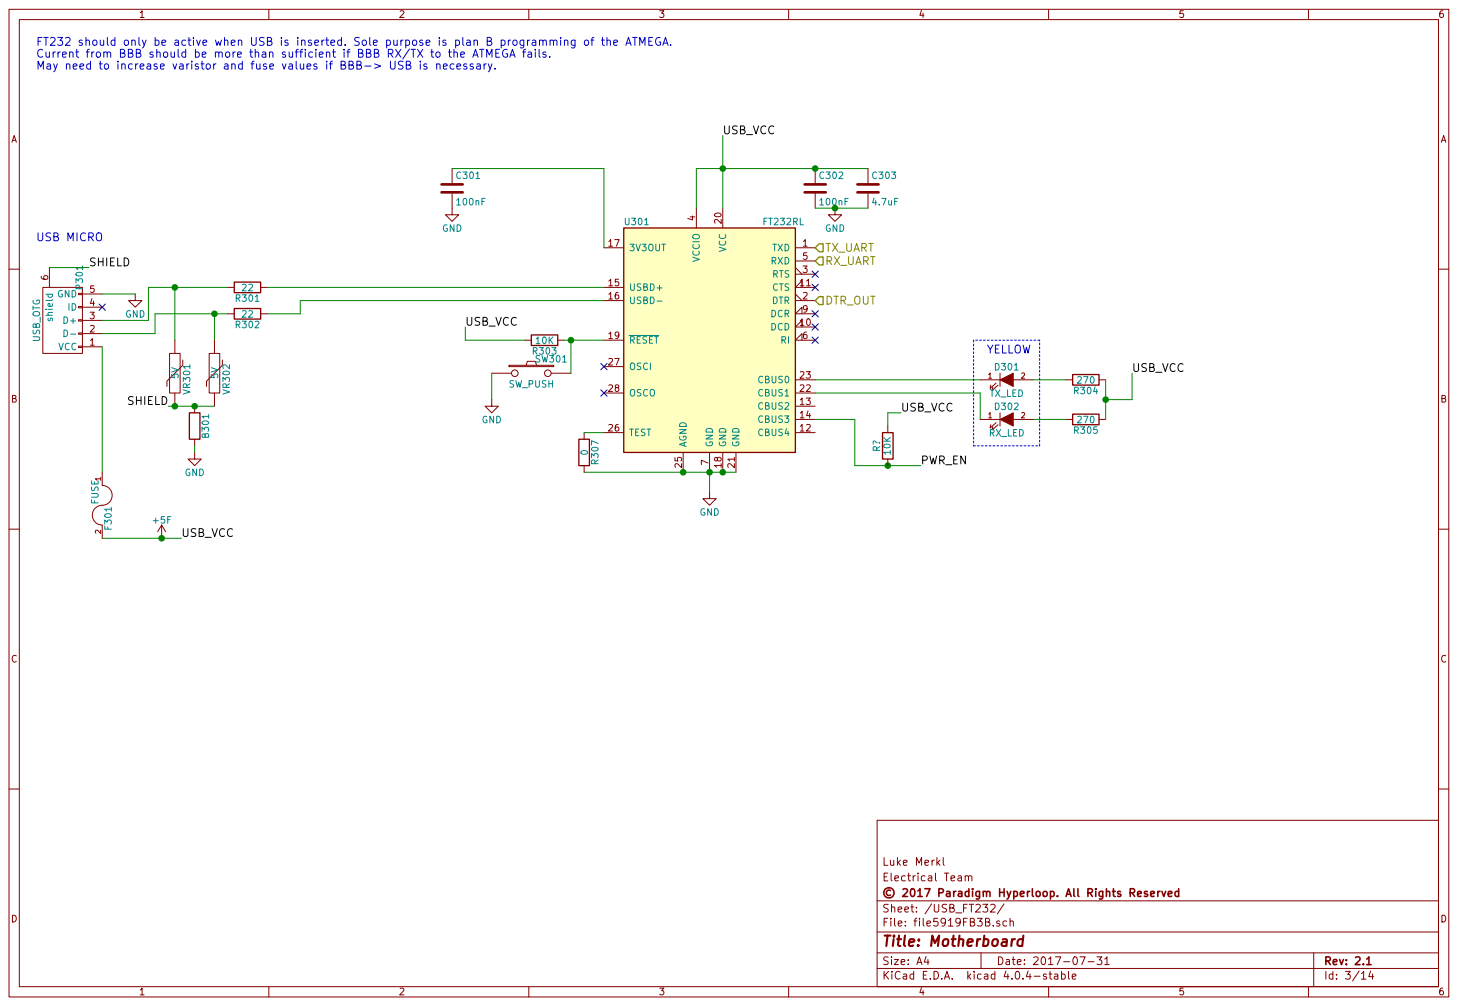
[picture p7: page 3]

FT232 should only be active when USB is inserted. Sole purpose is plan B programming of the ATMEGA.
Current from BBB should be more than sufficient if BBB RX/TX to the ATMEGA fails.

7 DCR 9 DCD 10 VCC 20 CTS 11 GND 21 CBUS4 12 CBUS1 22 CBUS2 13 CBUS0 23 CBUS3 14 USBD+ 15 AGND 25 USBD- 16 TEST 26

Luke Merkl
© 2017 Paradigm Hyperloop. All Rights Reserved Electrical Team

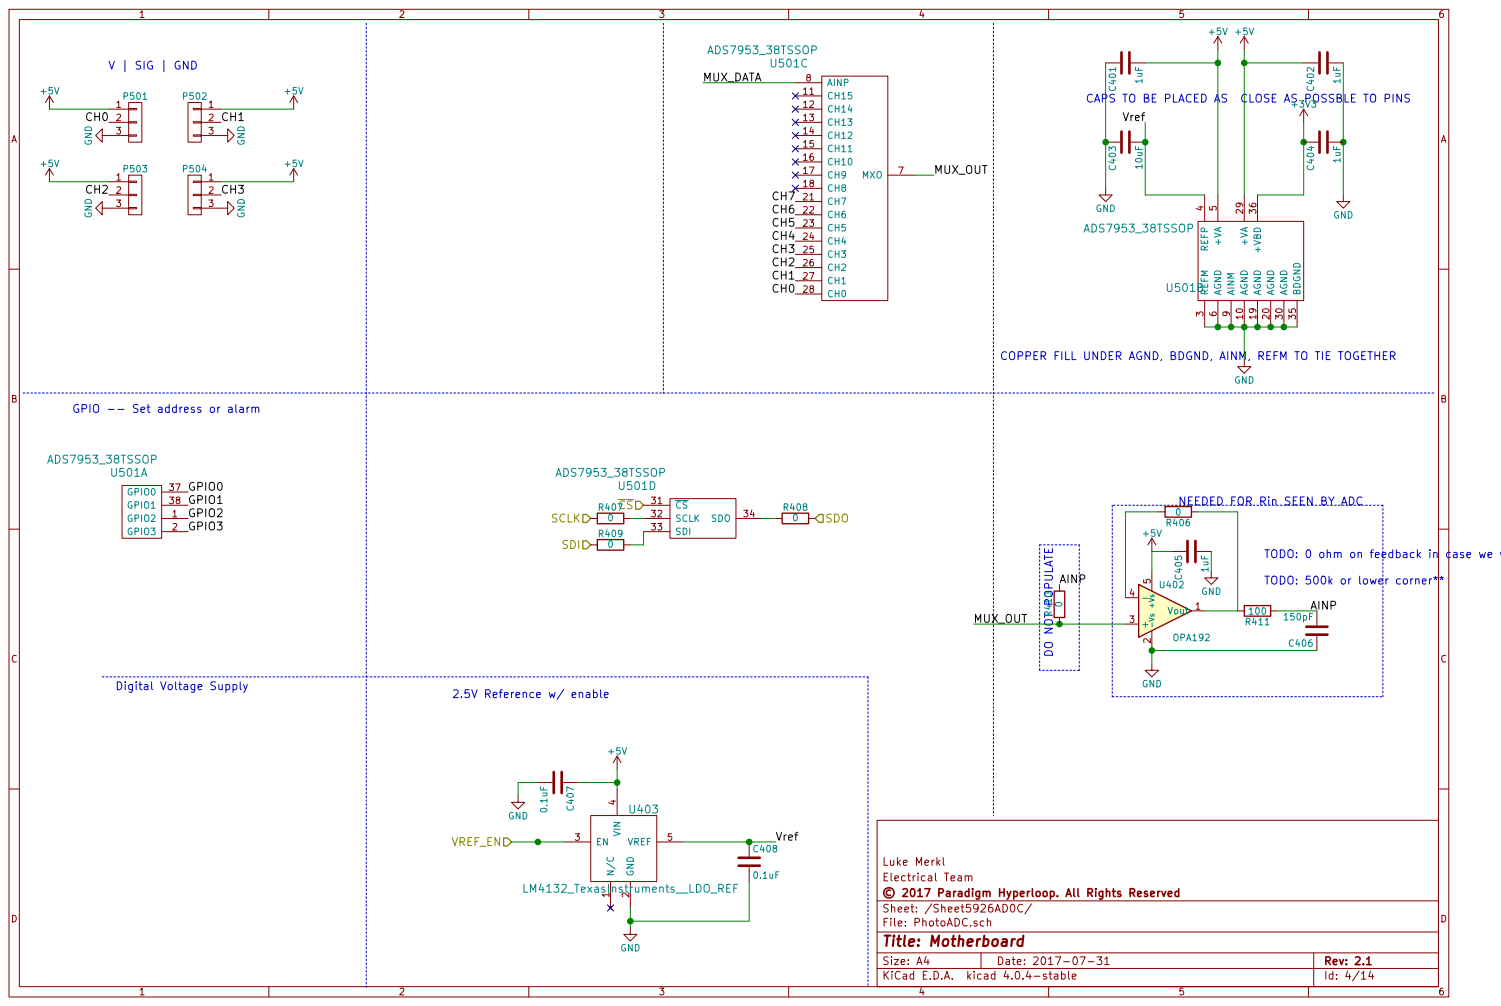
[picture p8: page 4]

CH3 GND GND GND GND

9 AGND 10 AGND 20 AGND 30 BDGND 35 +VBD 36 AGND 19 +VA 29 U501B

GPIO -- Set address or alarm

NEEDED FOR Rin SEEN BY ADC
TODO: 0 ohm on feedback in case we want to jump+filter R406

Luke Merkl
File: PhotoADC.sch Sheet: /Sheet5926AD0C/ © 2017 Paradigm Hyperloop. All Rights Reserved Electrical Team

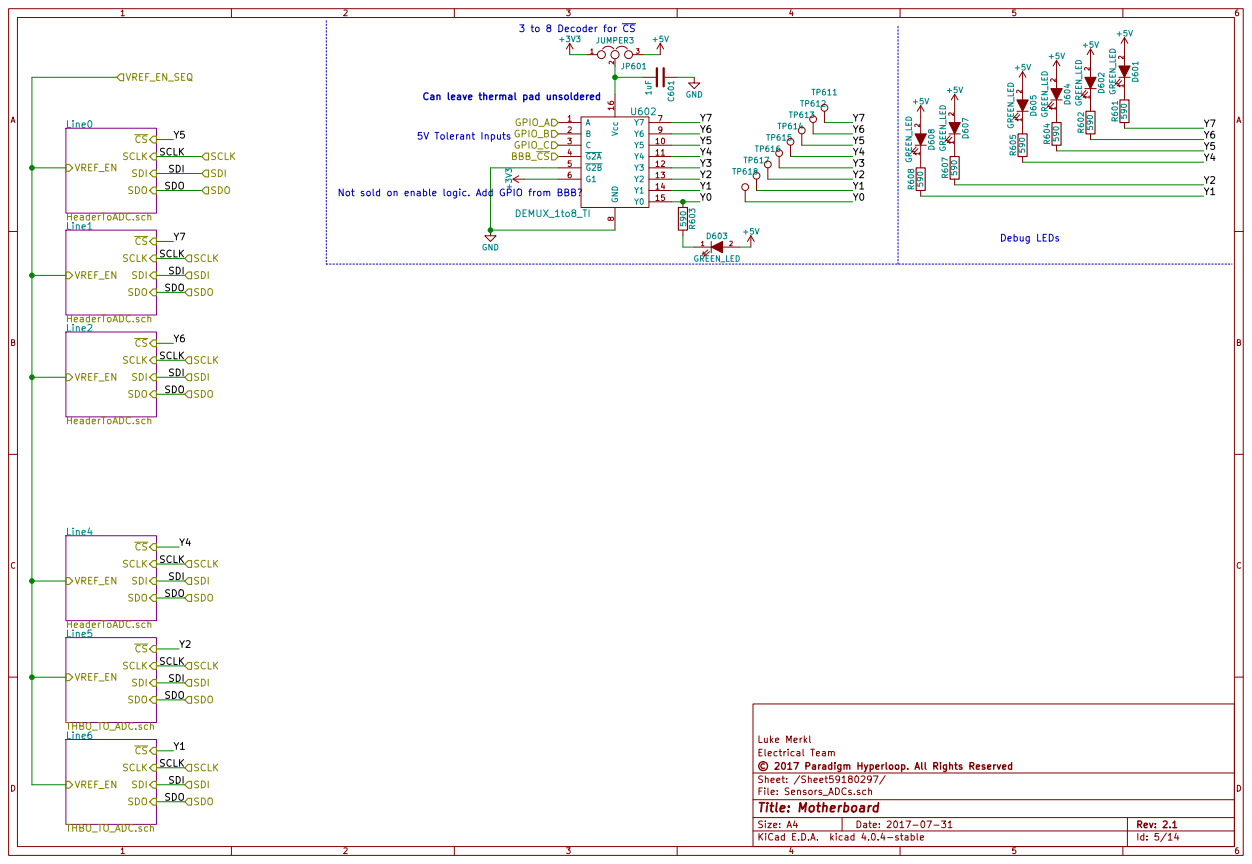
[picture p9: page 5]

3 to 8 Decoder for CS

Luke Merkl
File: Sensors_ADCs.sch Sheet: /Sheet59180297/ © 2017 Paradigm Hyperloop. All Rights Reserved Electrical Team

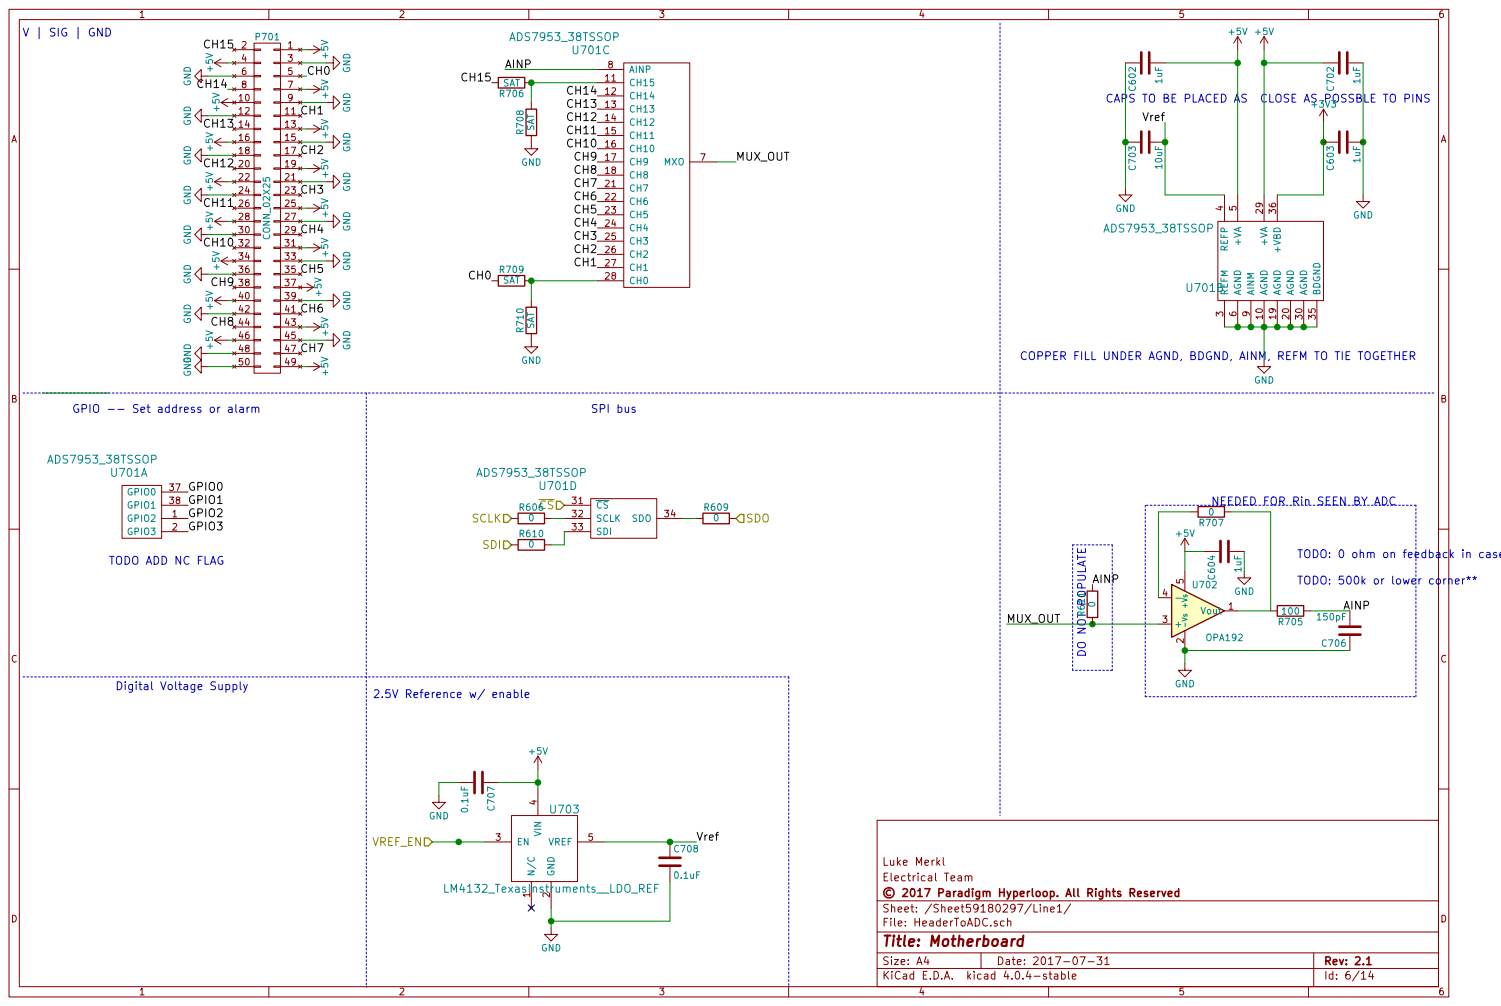
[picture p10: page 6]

+3V3 TODO: 500k or lower corner**

9 AGND 10 AGND 20 AGND 30 BDGND 35 +VBD 36 AGND 19 +VA 29 U701B

TODO: 0 ohm on feedback in case we want to jump+filter TODO ADD NC FLAG

Luke Merkl
File: HeaderToADC.sch Sheet: /Sheet59180297/Line1/ © 2017 Paradigm Hyperloop. All Rights Reserved Electrical Team

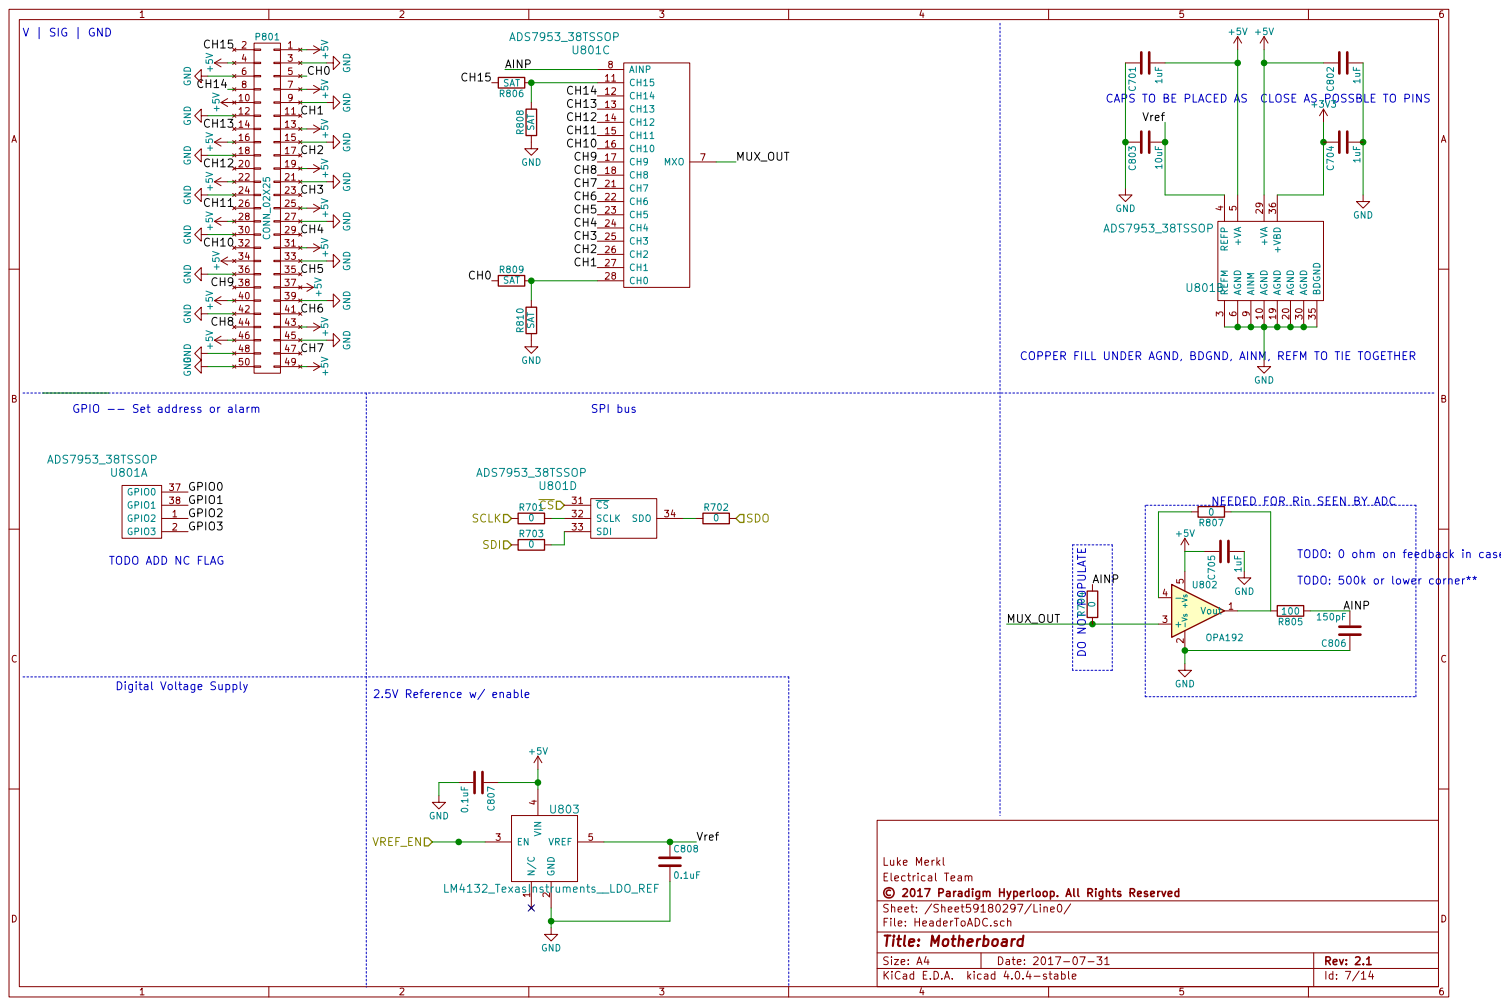
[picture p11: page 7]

+3V3 TODO: 500k or lower corner**

9 AGND 10 AGND 20 AGND 30 BDGND 35 +VBD 36 AGND 19 +VA 29 U801B

TODO: 0 ohm on feedback in case we want to jump+filter TODO ADD NC FLAG

Luke Merkl
File: HeaderToADC.sch Sheet: /Sheet59180297/Line0/ © 2017 Paradigm Hyperloop. All Rights Reserved Electrical Team

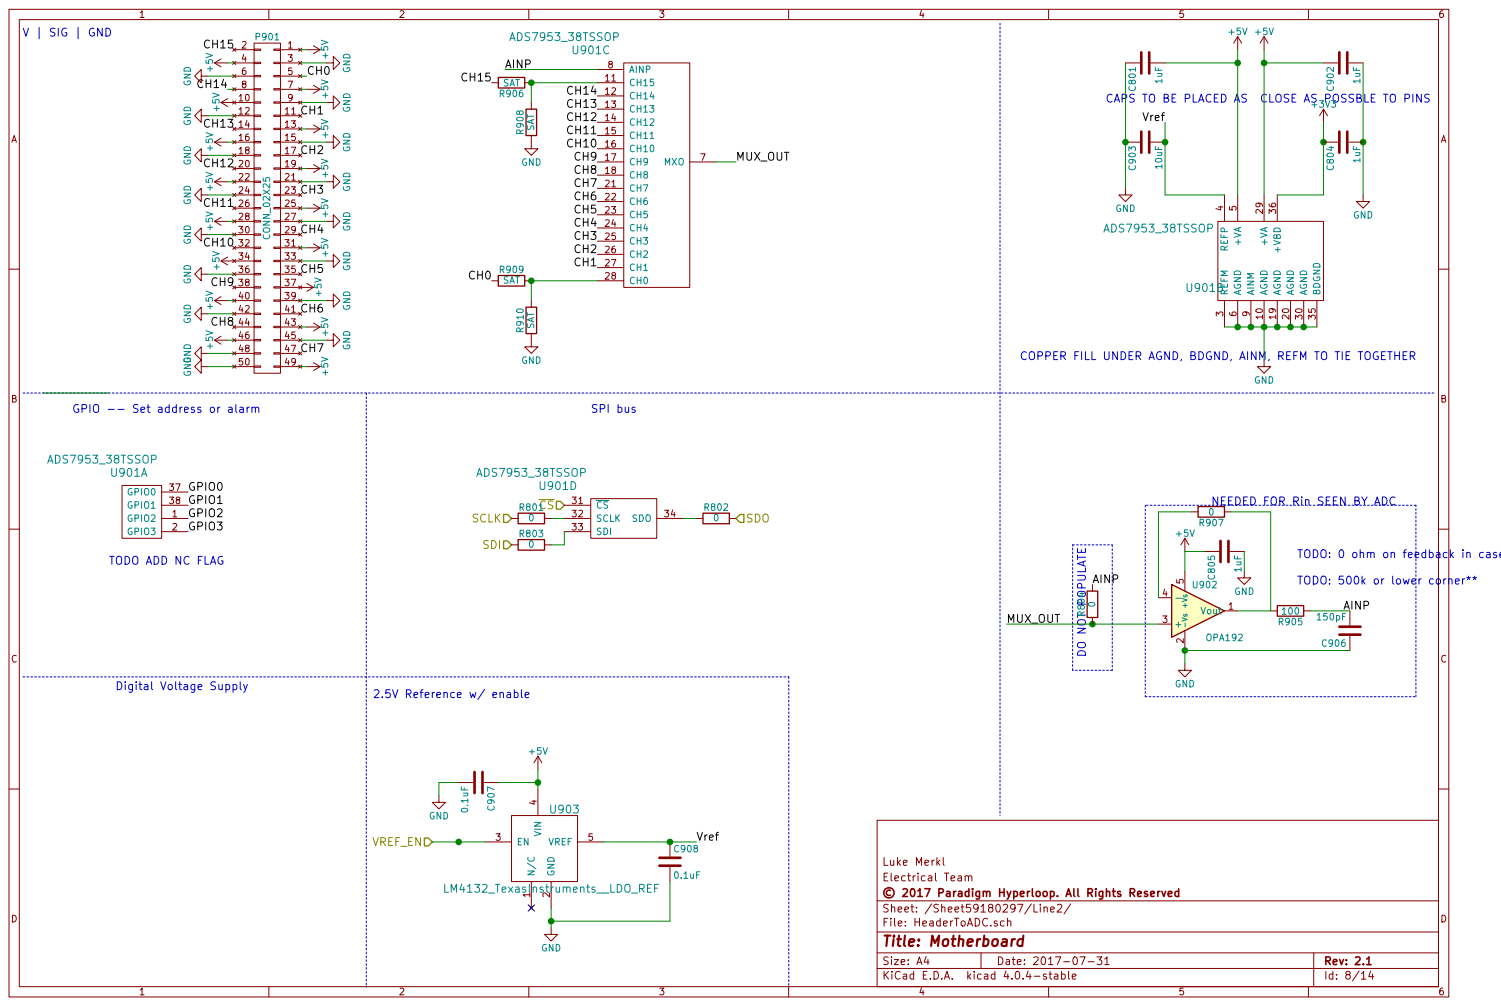
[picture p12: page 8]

+3V3 TODO: 500k or lower corner**

9 AGND 10 AGND 20 AGND 30 BDGND 35 +VBD 36 AGND 19 +VA 29 U901B

TODO: 0 ohm on feedback in case we want to jump+filter TODO ADD NC FLAG

Luke Merkl
File: HeaderToADC.sch Sheet: /Sheet59180297/Line2/ © 2017 Paradigm Hyperloop. All Rights Reserved Electrical Team

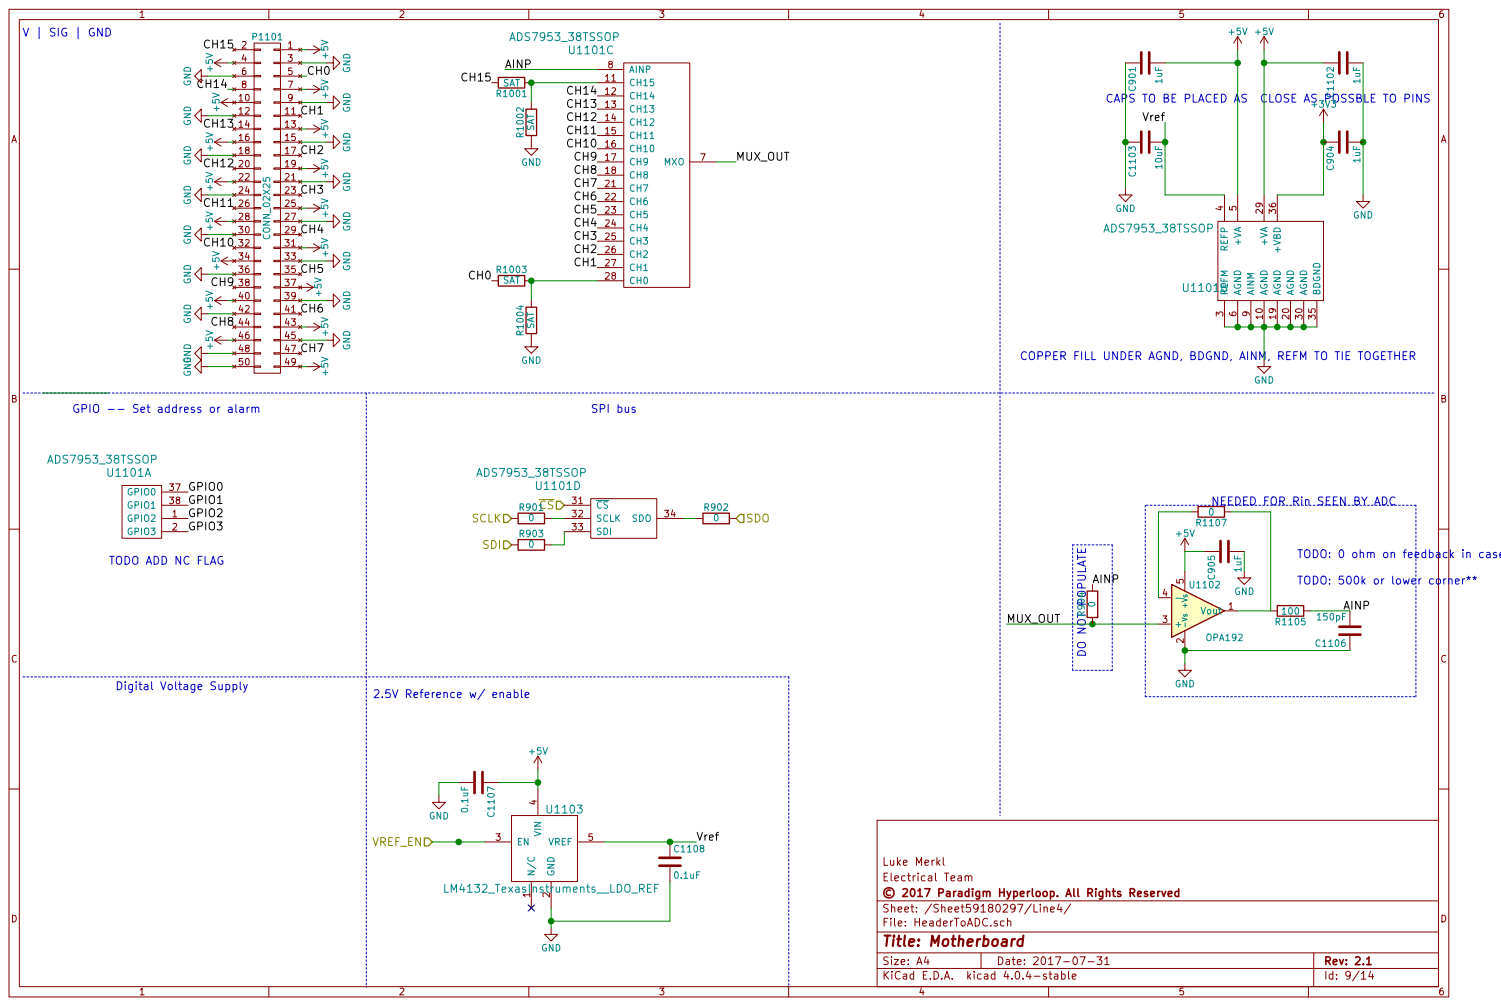
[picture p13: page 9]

+3V3 TODO: 500k or lower corner**

9 AGND 10 AGND 20 AGND 30 BDGND 35 +VBD 36 AGND 19 +VA 29 U1101B

TODO: 0 ohm on feedback in case we want to jump+filter TODO ADD NC FLAG

Luke Merkl
File: HeaderToADC.sch Sheet: /Sheet59180297/Line4/ © 2017 Paradigm Hyperloop. All Rights Reserved Electrical Team

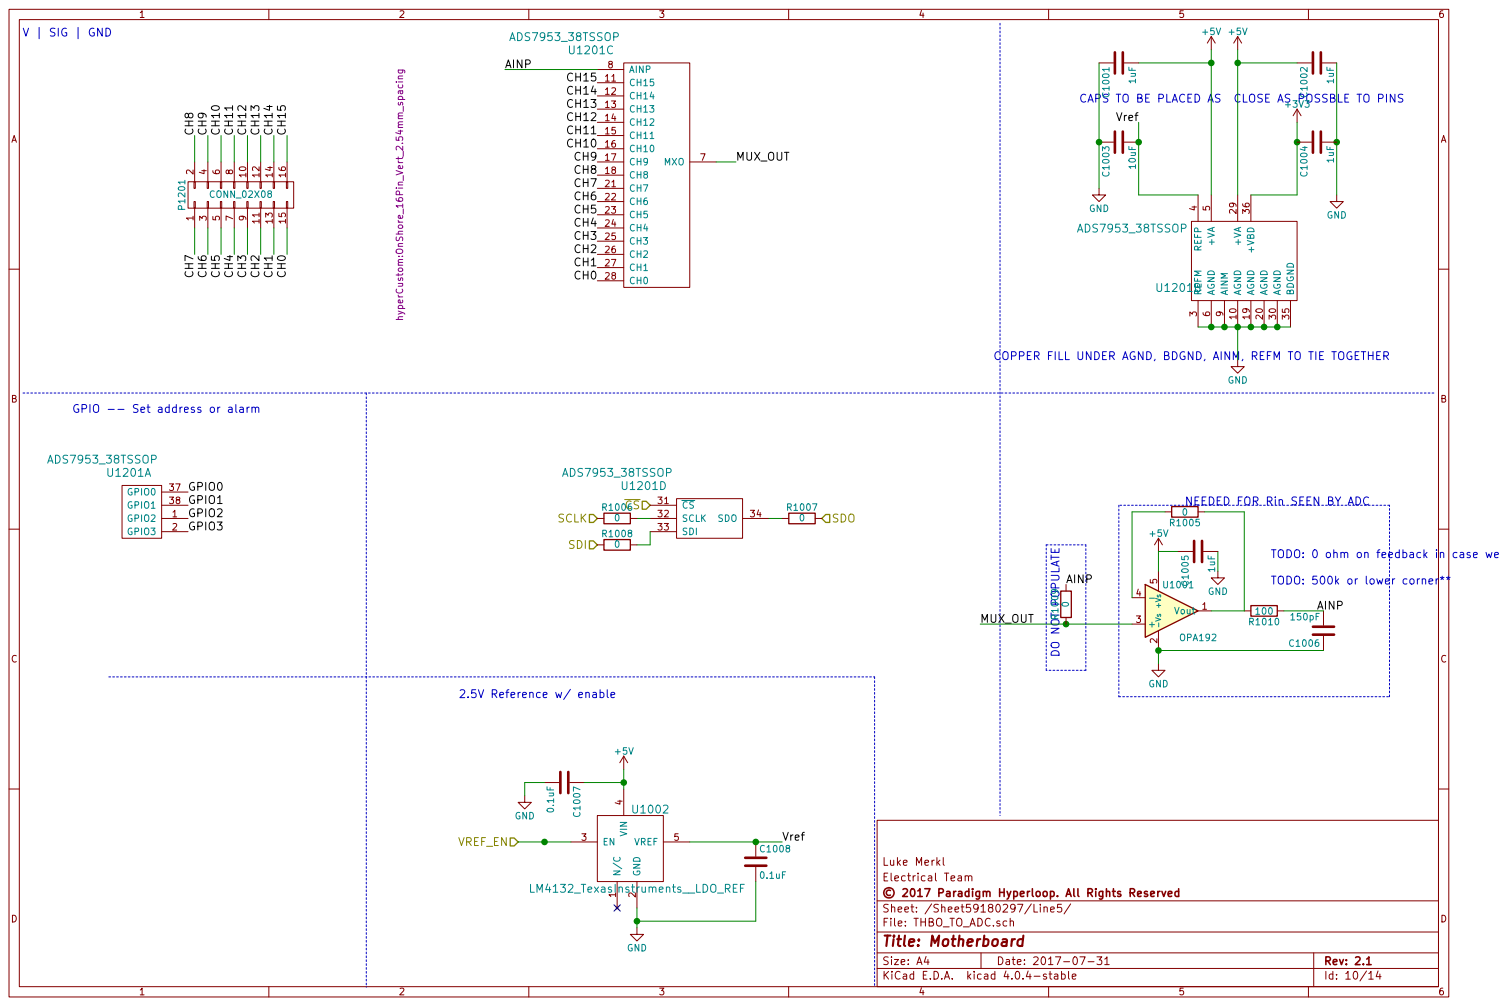
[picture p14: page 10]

+3V3 TODO: 500k or lower corner**

9 AGND 10 AGND 20 AGND 30 BDGND 35 +VBD 36 AGND 19 +VA 29 U1201B

GPIO -- Set address or alarm

NEEDED FOR Rin SEEN BY ADC
TODO: 0 ohm on feedback in case we want to jump+filter R1005

Luke Merkl
File: THBO_TO_ADC.sch Sheet: /Sheet59180297/Line5/ © 2017 Paradigm Hyperloop. All Rights Reserved Electrical Team

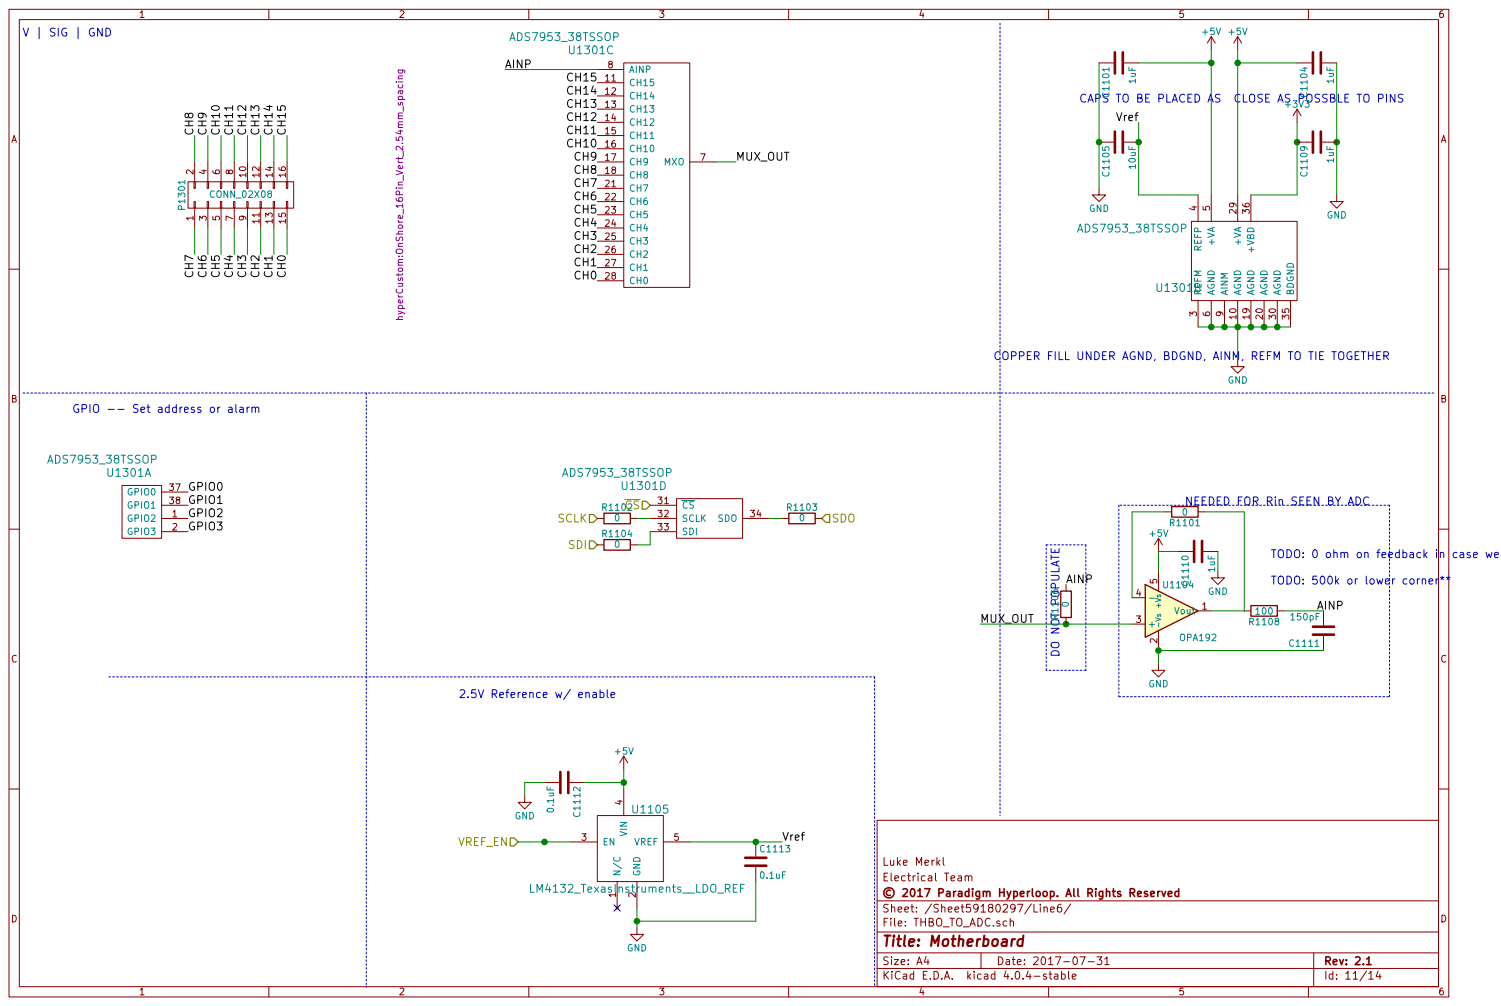
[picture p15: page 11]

+3V3 TODO: 500k or lower corner**

9 AGND 10 AGND 20 AGND 30 BDGND 35 +VBD 36 AGND 19 +VA 29 U1301B

GPIO -- Set address or alarm

NEEDED FOR Rin SEEN BY ADC
TODO: 0 ohm on feedback in case we want to jump+filter R1101

Luke Merkl
File: THBO_TO_ADC.sch Sheet: /Sheet59180297/Line6/ © 2017 Paradigm Hyperloop. All Rights Reserved Electrical Team

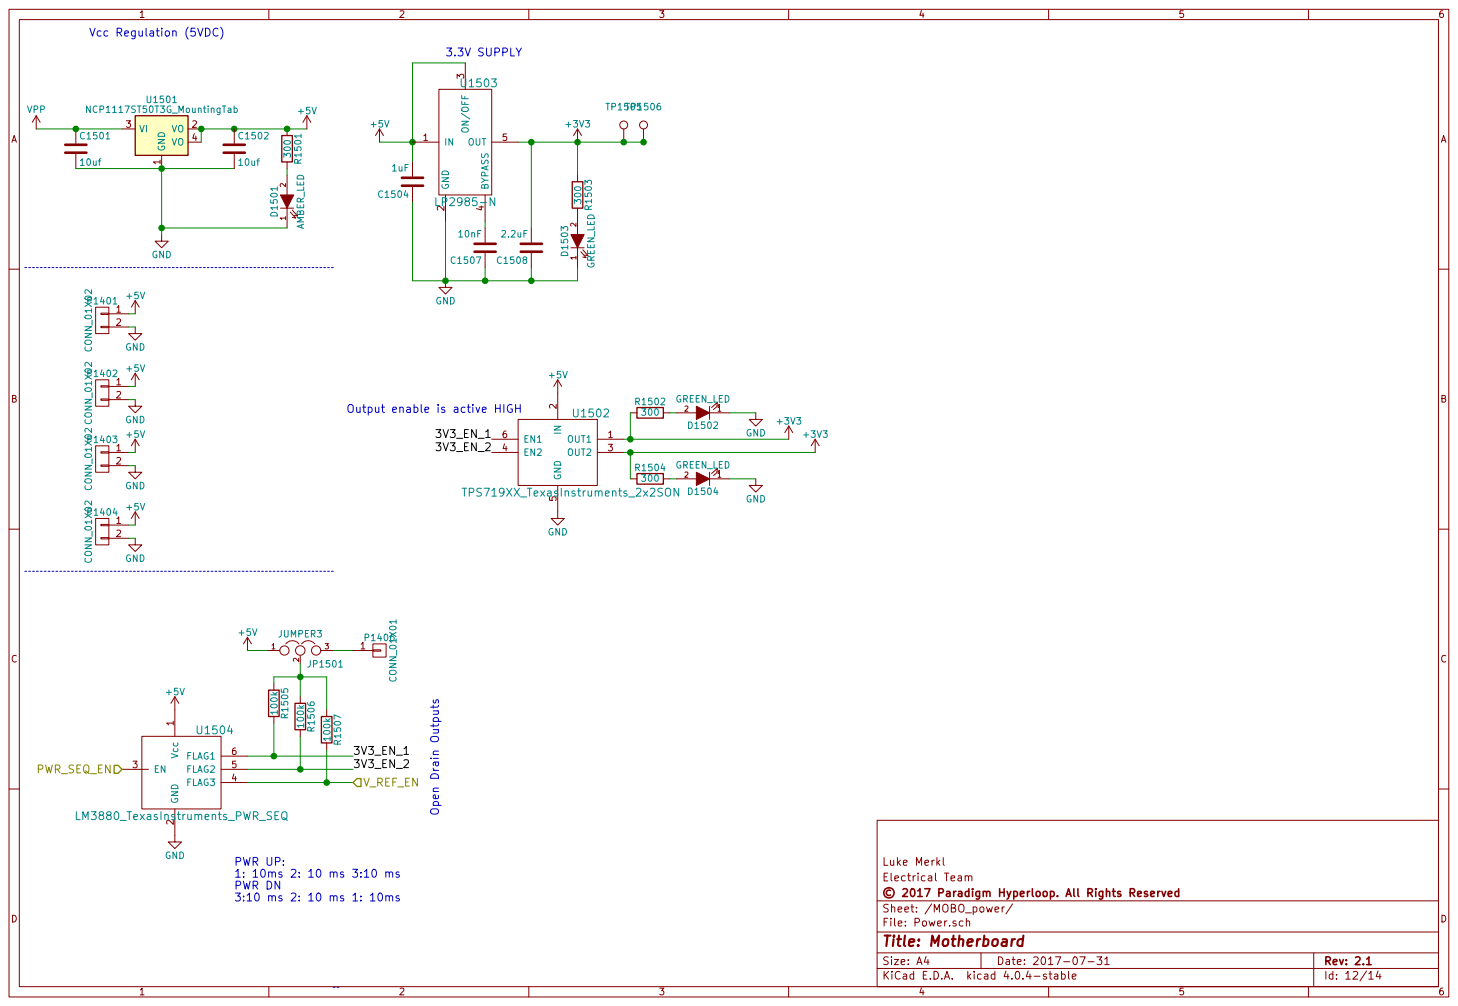
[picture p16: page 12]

Luke Merkl
© 2017 Paradigm Hyperloop. All Rights Reserved Electrical Team

File: Power.sch Sheet: /MOBO_power/
Id: 12/14 Title: Motherboard


Main power board connectors
NOTE: BBB_INT is 5V and BBB_ONOFF
is level shifted on MPB

Luke Merkl
File: Beaglebone_Black.sch Sheet: /Sheet592695A3/ © 2017 Paradigm Hyperloop. All Rights Reserved Electrical Team


2 MCLK 3 MO 4 MI 5 MSS 6 VIA 7 VOB 8 DCLK 9 GND1 10 VDD2 20 GND2 11 NIC 12 VIB 13 VOA 14 SSS 15 SO 16 SI 17 SCLK 18 GND2 19 U1304 ADuM3150_AnalogDev_7CH_ISO

IS01541 has clock Master --> slave only

Luke Merkl
File: Isolation.sch Sheet: /Sheet592896E3/ © 2017 Paradigm Hyperloop. All Rights Reserved Electrical Team

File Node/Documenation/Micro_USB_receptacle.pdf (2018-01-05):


PDS: Rev :D STATUS:Released Printed: May 16, 2017


PDS: Rev :D STATUS:Released Printed: May 16, 2017

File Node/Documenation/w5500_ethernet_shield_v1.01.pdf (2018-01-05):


2015-06-11 오후 5:00:15 f=0.50 D:\Wiznet\Schematic\W5500_Ethernet_shield_V1.01_sch\W5500_Ethernet_shield_v1.01.sch (Sheet: 1/2)


2015-06-11 오후 5:00:15 f=0.50 D:\Wiznet\Schematic\W5500_Ethernet_shield_V1.01_sch\W5500_Ethernet_shield_v1.01.sch (Sheet: 2/2)














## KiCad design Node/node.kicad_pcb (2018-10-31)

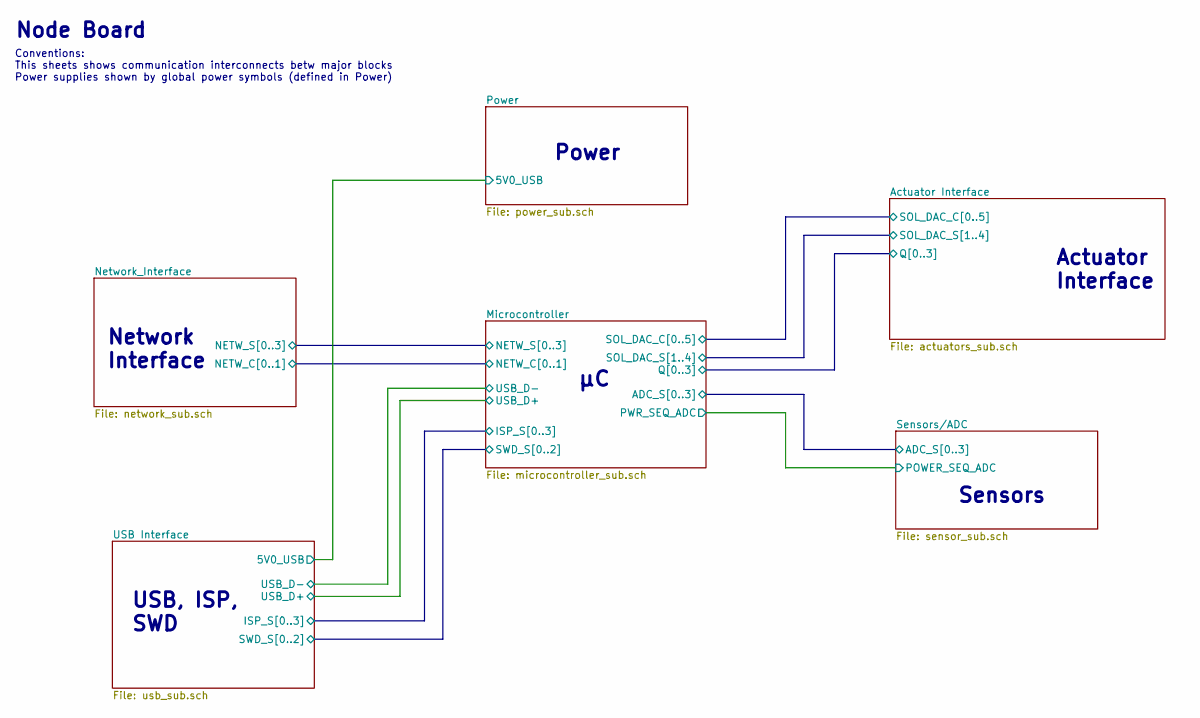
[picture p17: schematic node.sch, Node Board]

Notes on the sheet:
Network Interface
Actuator Interface
Power
Sensors
Node Board
USB, ISP, SWD
Conventions: This sheets shows communication interconnects betw major blocks Power supplies shown by global power symbols (defined in Power)

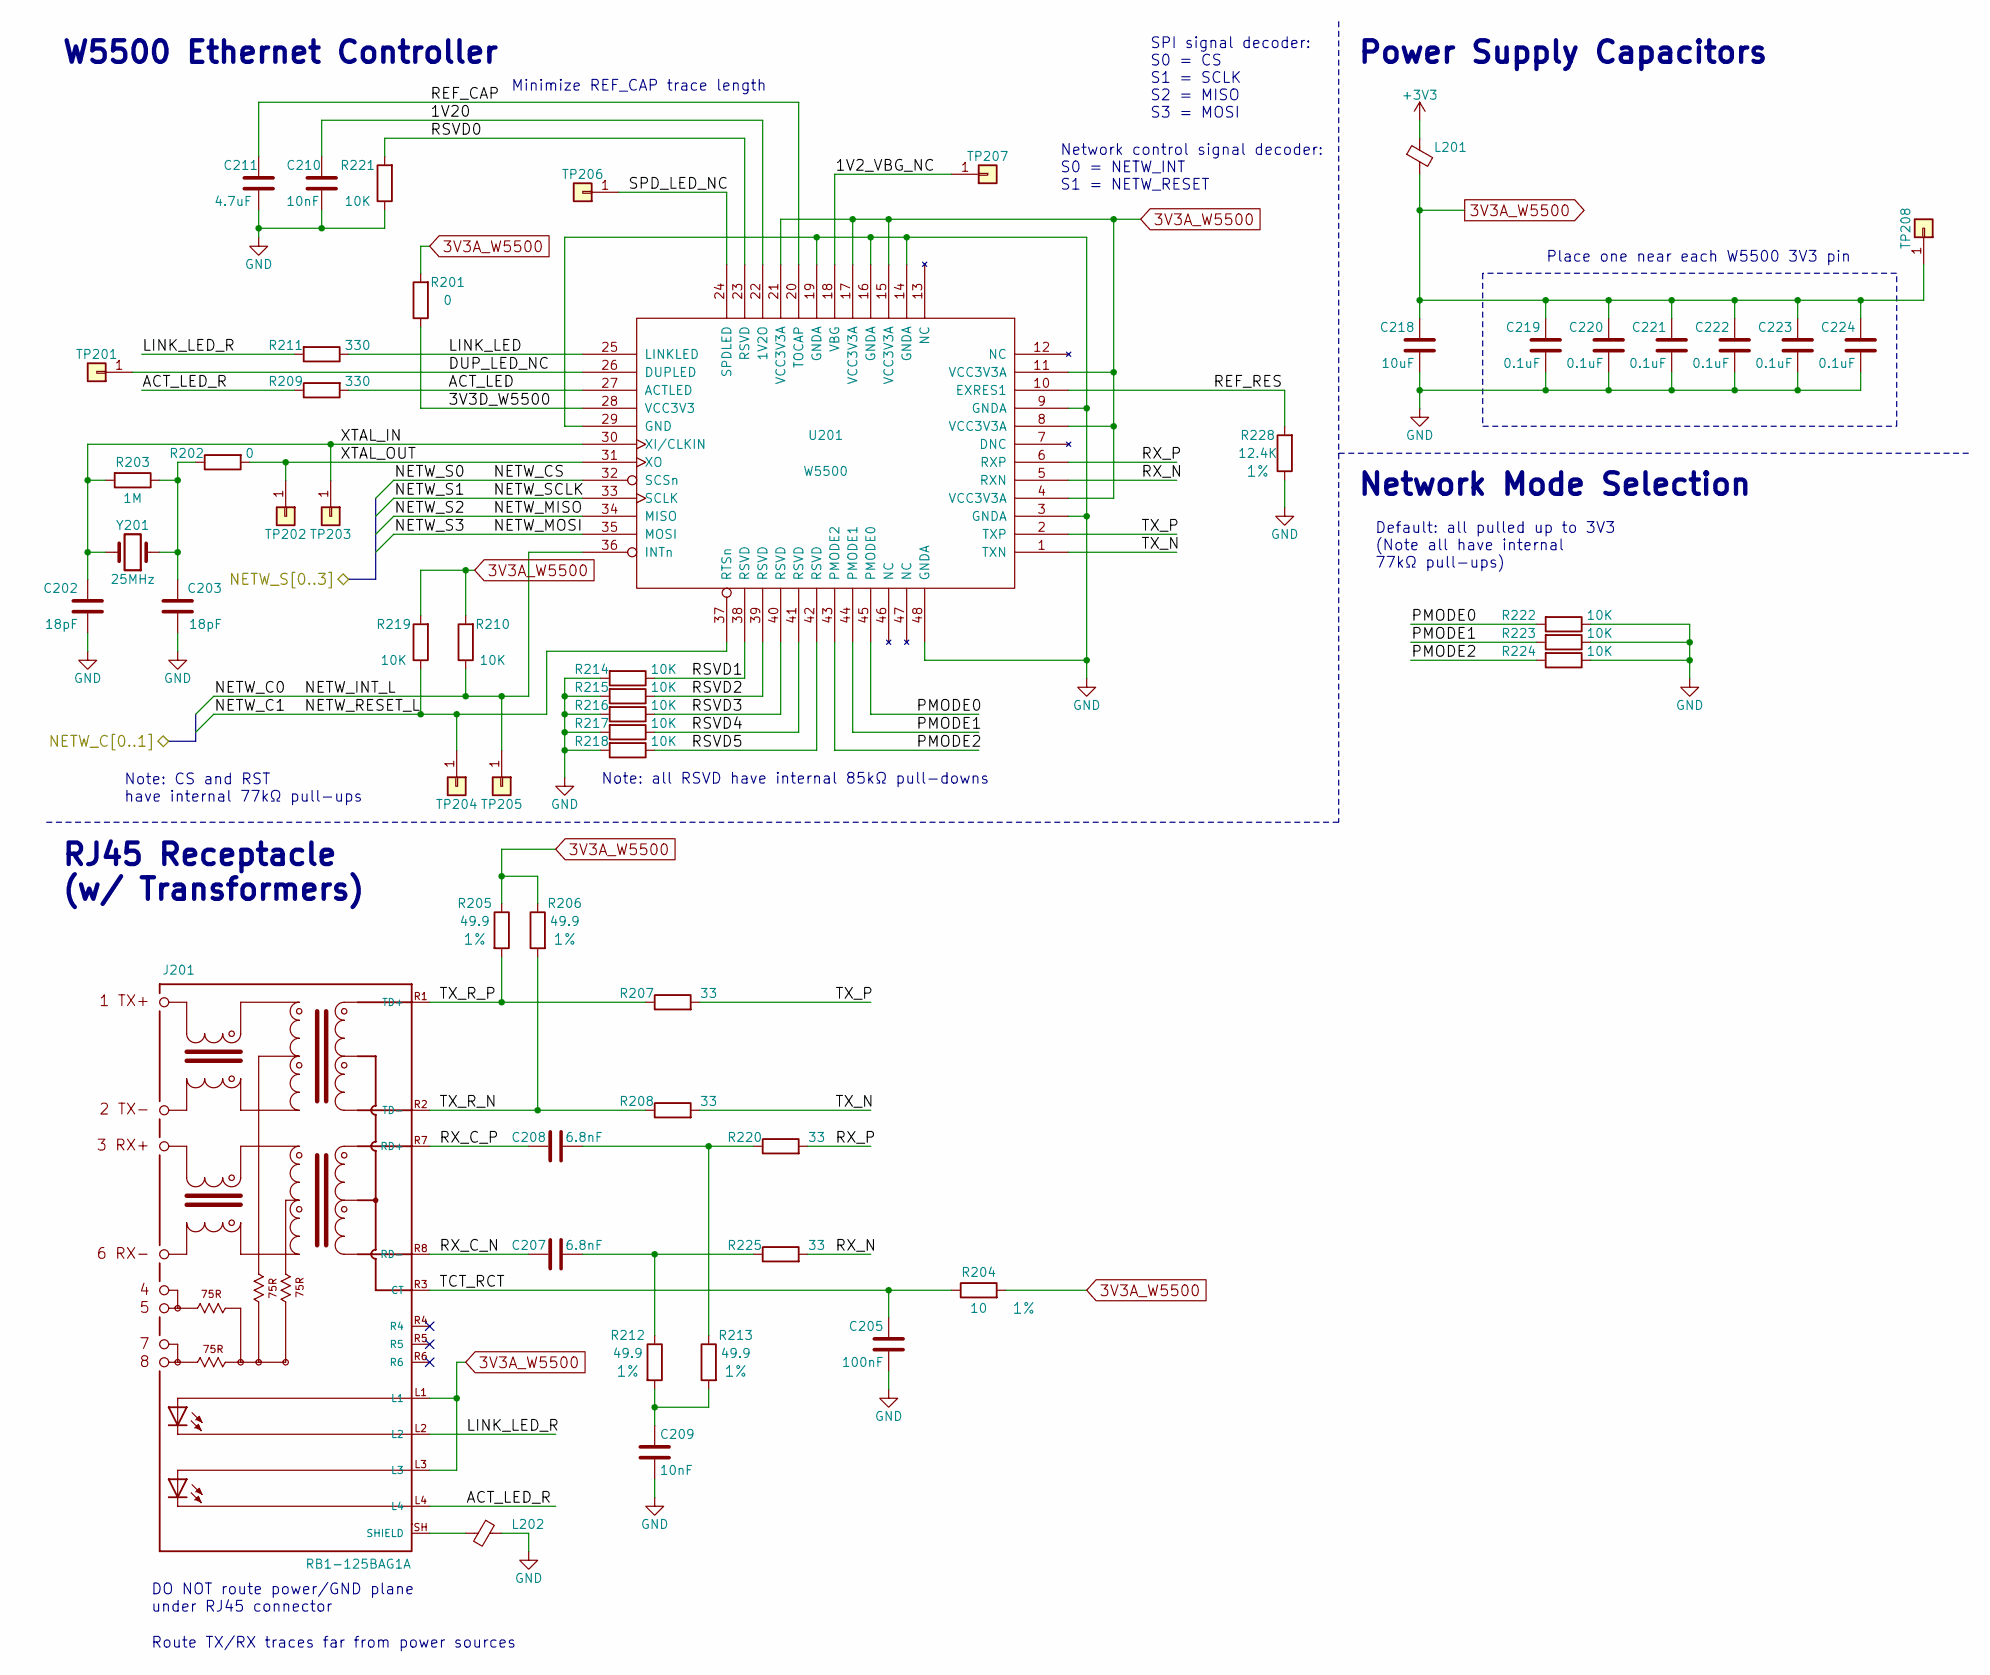
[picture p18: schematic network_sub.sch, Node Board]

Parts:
C202, C203: 18pF; C_0805_HandSoldering
C205: 100nF; C_0805_HandSoldering
C207, C208: 6.8nF; C_0805_HandSoldering
C209, C210: 10nF; C_0805_HandSoldering
C211: 4.7uF; C_0805_HandSoldering
C218: 10uF; C_0805_HandSoldering
C219, C220, C221, C222, C223, C224: 0.1uF; C_0805_HandSoldering
J201: RB1-125BAG1A; WIZNET_RB1-125BAG1A; Mfg. Part Num RB1-125BAG1A
L201, L202: Ferrite_Bead_Small; R_1206_HandSoldering
R201: 0; R_1206_HandSoldering
R202: 0; R_0805_HandSoldering
R203: 1M; R_0805_HandSoldering
R204: 10; R_0805_HandSoldering; Tolerance 1%
R205, R206, R212, R213: 49.9; R_0805_HandSoldering; Tolerance 1%; Mfg. Part Num RC0805FR-0749R9L
R207, R208, R220, R225: 33; R_0805_HandSoldering; Mfg. Part Num RC0805FR-0733RL
R209, R211: 330; R_0805_HandSoldering
R210, R214, R215, R216, R217, R218, R219, R221, R222, R223, R224: 10K; R_0805_HandSoldering
R228: 12.4K; R_0805_HandSoldering; Tolerance 1%; Mfg. Part Num RC0805FR-0712K4L
TP201, TP202, TP203, TP204, TP205, TP206, TP207, TP208: Conn_01x01; Testpoint_circle_0.5mm
U201: W5500; LQFP-48_7x7mm_Pitch0.5mm; Mfg. Part Num W5500
Y201: 25MHz; Murata_25MHz_XTAL_XRCGB25M000F3M00R0; Mfg. Part Num XRCGB25M000F3M00R0

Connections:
3V3A_W5500: C218.1, C219.1, C220.1, C221.1, C222.1, C223.1, C224.1, J201.L1, J201.L3, L201.2, R201.2, R204.2, R205.1, R206.1, R210.2, R219.2, TP208.1, U201.4 (VCC3V3A), U201.8 (VCC3V3A), U201.11 (VCC3V3A), U201.15 (VCC3V3A), U201.17 (VCC3V3A), U201.21 (VCC3V3A)
+3V3: L201.1; also elsewhere on the board
/Microcontroller/NETW_C0: R210.1, TP205.1, U201.36 (INTn); also elsewhere on the board
/Microcontroller/NETW_C1: R219.1, TP204.1, U201.37 (RTSn); also elsewhere on the board
/Microcontroller/NETW_CS: U201.32 (SCSn); also elsewhere on the board
/Microcontroller/NETW_MISO: U201.34 (MISO); also elsewhere on the board
/Microcontroller/NETW_MOSI: U201.35 (MOSI); also elsewhere on the board
/Microcontroller/NETW_S1: U201.33 (SCLK); also elsewhere on the board
/Network_Interface/1V2_VBG_NC: TP207.1, U201.18 (VBG)
/Network_Interface/1V20: C210.1, U201.22 (1V2O)
/Network_Interface/3V3D_W5500: R201.1, U201.28 (VCC3V3)
/Network_Interface/ACT_LED: R209.2, U201.27 (ACTLED)
/Network_Interface/ACT_LED_R: J201.L4, R209.1
/Network_Interface/DUP_LED_NC: TP201.1, U201.26 (DUPLED)
/Network_Interface/LINK_LED: R211.1, U201.25 (LINKLED)
/Network_Interface/LINK_LED_R: J201.L2, R211.2
/Network_Interface/PMODE0: R222.2, U201.45 (PMODE0)
/Network_Interface/PMODE1: R223.2, U201.44 (PMODE1)
/Network_Interface/PMODE2: R224.2, U201.43 (PMODE2)
/Network_Interface/REF_CAP: C211.1, U201.20 (TOCAP)
/Network_Interface/REF_RES: R228.2, U201.10 (EXRES1)
/Network_Interface/RSVD0: R221.2, U201.23 (RSVD)
/Network_Interface/RSVD1: R214.1, U201.38 (RSVD)
/Network_Interface/RSVD2: R215.1, U201.39 (RSVD)
/Network_Interface/RSVD3: R216.1, U201.40 (RSVD)
/Network_Interface/RSVD4: R217.1, U201.41 (RSVD)
/Network_Interface/RSVD5: R218.1, U201.42 (RSVD)
/Network_Interface/RX_C_N: C207.2, J201.R8 (RD-)
/Network_Interface/RX_C_P: C208.2, J201.R7 (RD+)
/Network_Interface/RX_N: R225.2, U201.5 (RXN)
/Network_Interface/RX_P: R220.2, U201.6 (RXP)
/Network_Interface/SPD_LED_NC: TP206.1, U201.24 (SPDLED)
/Network_Interface/TCT_RCT: C205.1, J201.R3 (CT), R204.1
/Network_Interface/TX_N: R208.2, U201.1 (TXN)
/Network_Interface/TX_P: R207.2, U201.2 (TXP)
/Network_Interface/TX_R_N: J201.R2 (TD-), R206.2, R208.1
/Network_Interface/TX_R_P: J201.R1 (TD+), R205.2, R207.1
/Network_Interface/XTAL_IN: C202.2, R203.2, TP203.1, U201.30 (XI/CLKIN), Y201.2
/Network_Interface/XTAL_OUT: R202.2, TP202.1, U201.31 (XO)
GND: C202.1, C203.1, C205.2, C209.2, C210.2, C211.2, C218.2, C219.2, C220.2, C221.2, C222.2, C223.2, C224.2, L202.1, R214.2, R215.2, R216.2, R217.2, R218.2, R221.1, R222.1, R223.1, R224.1, R228.1, U201.3 (GNDA), U201.9 (GNDA), U201.14 (GNDA), U201.16 (GNDA), U201.19 (GNDA), U201.29 (GND), U201.48 (GNDA); also elsewhere on the board
unnamed: C203.2, R202.1, R203.1, Y201.1
unnamed: C207.1, R212.1, R225.1
unnamed: C208.1, R213.1, R220.1
unnamed: C209.1, R212.2, R213.2
unnamed: J201.SH (SHIELD), L202.2

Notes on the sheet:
RJ45 Receptacle (w/ Transformers)
W5500 Ethernet Controller
Power Supply Capacitors
Place one near each W5500 3V3 pin
Network Mode Selection
Default: all pulled up to 3V3 (Note all have internal 77kΩ pull-ups)
Minimize REF_CAP trace length
Note: all RSVD have internal 85kΩ pull-downs
Note: CS and RST have internal 77kΩ pull-ups
DO NOT route power/GND plane under RJ45 connector
Route TX/RX traces far from power sources
SPI signal decoder: S0 = CS S1 = SCLK S2 = MISO S3 = MOSI
Network control signal decoder: S0 = NETW_INT S1 = NETW_RESET

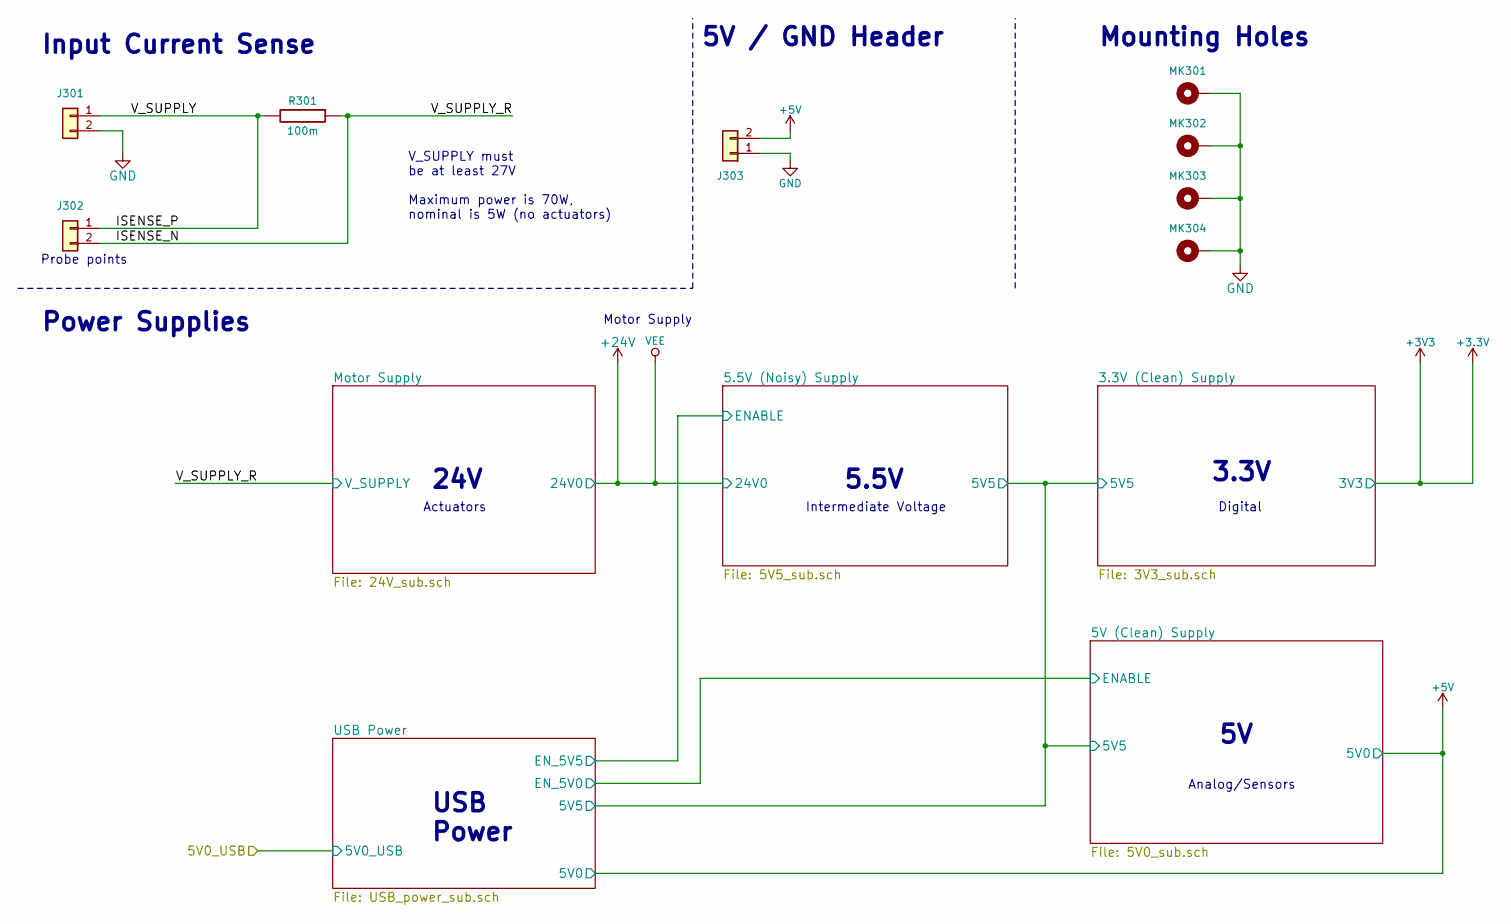
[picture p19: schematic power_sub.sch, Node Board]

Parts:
J301: CONN_01X02; Molex_2pin_power_0010844022; MFG. P/N 0010844022
J302, J303: CONN_01X02; Pin_Header_Straight_1x02_Pitch2.54mm; MFG. P/N PPTC021LFBN-RC
MK301, MK302, MK303, MK304: Mounting_Hole_PAD; MountingHole_M3x0.5_3.5mm_hole
R301: 100m; R_2512_HandSoldering; Mfg. Part Num CRA2512-FZ-R100ELF

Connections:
+5V: J303.2; also elsewhere on the board
/Power/ISENSE_N: J302.2, R301.1; also elsewhere on the board
/Power/ISENSE_P: J301.1, J302.1, R301.2
GND: J301.2, J303.1, MK301.1, MK302.1, MK303.1, MK304.1; also elsewhere on the board

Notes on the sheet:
24V
5.5V
3.3V
Digital
Analog/Sensors
Intermediate Voltage
Actuators
Motor Supply
USB Power
V_SUPPLY must be at least 27V Maximum power is 70W, nominal is 5W (no actuators)
Power Supplies
Input Current Sense
Probe points
Mounting Holes
5V / GND Header

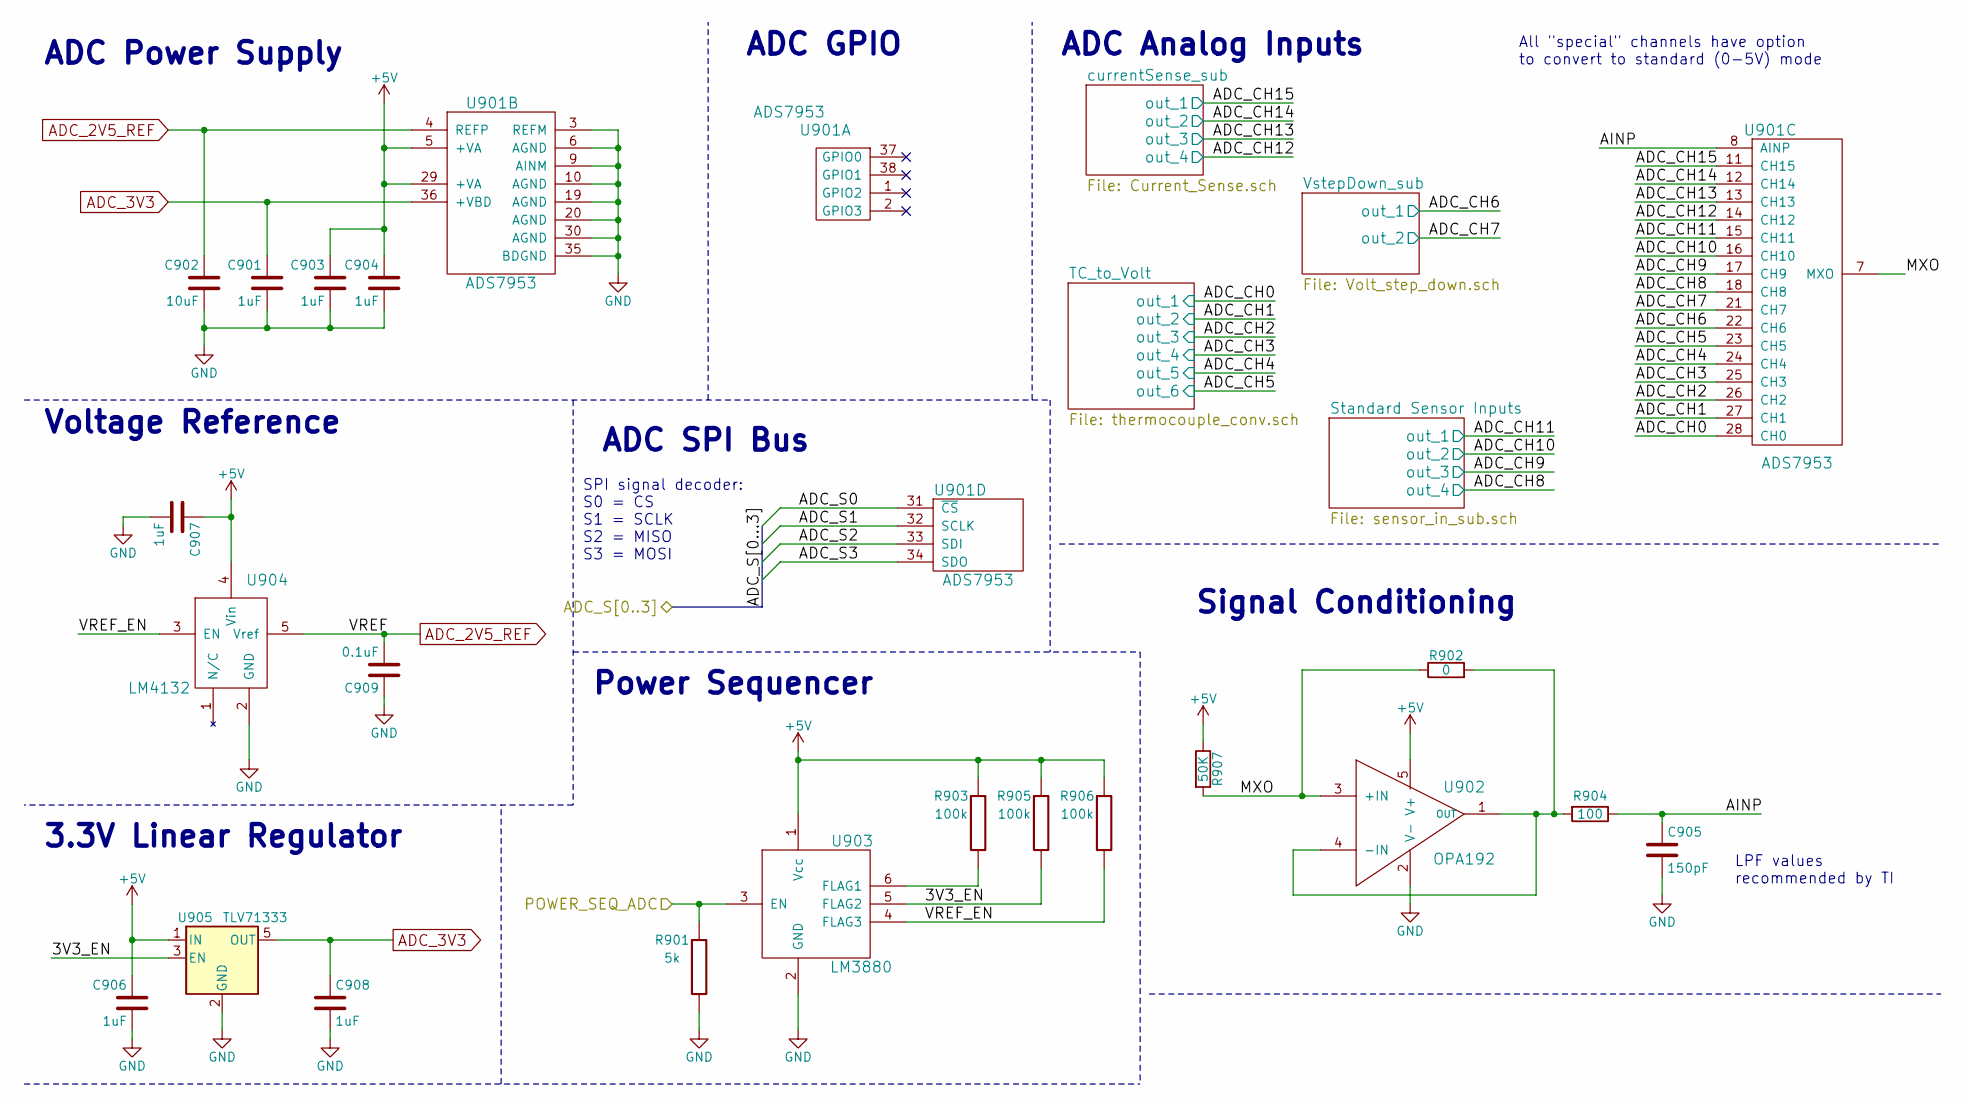
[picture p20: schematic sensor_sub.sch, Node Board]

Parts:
C901, C903, C904, C906, C907, C908: 1uF; C_0805_HandSoldering
C902: 10uF; C_0805_HandSoldering
C905: 150pF; C_0805_HandSoldering
C909: 0.1uF; C_0805_HandSoldering
R901: 5k; R_0805_HandSoldering
R902: 0; R_0805_HandSoldering
R903, R905, R906: 100k; R_0805_HandSoldering
R904: 100; R_0805_HandSoldering
R907: 50K; R_0805_HandSoldering
U901: ADS7953; TSSOP-38_4.4x9.7mm_Pitch0.5mm
U902: OPA192; SOT-23-5; Mfr P/N OPA192IDBVR
U903: LM3880; SOT-23-6_Handsoldering; Manufacturer P/N LM3880MF-1AA/NOPB
U904: LM4132; SOT-23-5; Manufacturer P/N LM4132BMF-2.5/NOPB
U905: TLV71333; SOT-23-5; Mfg. Part Num TLV71333PDBV

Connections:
+5V: C903.1, C904.1, C906.1, C907.1, R903.1, R905.1, R906.1, R907.1, U901.5 (+VA), U901.29 (+VA), U902.5 (V+), U903.1 (Vcc), U904.4 (Vin), U905.1 (IN); also elsewhere on the board
/Microcontroller/ADC_CS: U901.31 (~CS); also elsewhere on the board
/Microcontroller/ADC_MISO: U901.33 (SDI); also elsewhere on the board
/Microcontroller/ADC_MOSI: U901.34 (SDO); also elsewhere on the board
/Microcontroller/ADC_S1: U901.32 (SCLK); also elsewhere on the board
/Sensors/ADC/3V3_EN: R905.2, U903.5 (FLAG2), U905.3 (EN)
/Sensors/ADC/ADC_CH0: U901.28 (CH0); also elsewhere on the board
/Sensors/ADC/ADC_CH1: U901.27 (CH1); also elsewhere on the board
/Sensors/ADC/ADC_CH2: U901.26 (CH2); also elsewhere on the board
/Sensors/ADC/ADC_CH3: U901.25 (CH3); also elsewhere on the board
/Sensors/ADC/ADC_CH4: U901.24 (CH4); also elsewhere on the board
/Sensors/ADC/ADC_CH5: U901.23 (CH5); also elsewhere on the board
/Sensors/ADC/ADC_CH6: U901.22 (CH6); also elsewhere on the board
/Sensors/ADC/ADC_CH7: U901.21 (CH7); also elsewhere on the board
/Sensors/ADC/ADC_CH8: U901.18 (CH8); also elsewhere on the board
/Sensors/ADC/ADC_CH9: U901.17 (CH9); also elsewhere on the board
/Sensors/ADC/ADC_CH10: U901.16 (CH10); also elsewhere on the board
/Sensors/ADC/ADC_CH11: U901.15 (CH11); also elsewhere on the board
/Sensors/ADC/ADC_CH12: U901.14 (CH12); also elsewhere on the board
/Sensors/ADC/ADC_CH13: U901.13 (CH13); also elsewhere on the board
/Sensors/ADC/ADC_CH14: U901.12 (CH14); also elsewhere on the board
/Sensors/ADC/ADC_CH15: U901.11 (CH15); also elsewhere on the board
/Sensors/ADC/AINP: C905.1, R904.1, U901.8 (AINP)
/Sensors/ADC/MXO: R902.1, R907.2, U901.7 (MXO), U902.3 (+IN)
/Sensors/ADC/POWER_SEQ_ADC: R901.1, U903.3 (EN); also elsewhere on the board
/Sensors/ADC/VREF_EN: R906.2, U903.4 (FLAG3), U904.3 (EN)
ADC_2V5_REF: C902.1, C909.2, U901.4 (REFP), U904.5 (Vref)
ADC_3V3: C901.1, C908.1, U901.36 (+VBD), U905.5 (OUT)
GND: C901.2, C902.2, C903.2, C904.2, C905.2, C906.2, C907.2, C908.2, C909.1, R901.2, U901.3 (REFM), U901.6 (AGND), U901.9 (AINM), U901.10 (AGND), U901.19 (AGND), U901.20 (AGND), U901.30 (AGND), U901.35 (BDGND), U902.2 (V-), U903.2 (GND), U904.2 (GND), U905.2 (GND); also elsewhere on the board
unnamed: R902.2, R904.2, U902.1 (OUT), U902.4 (-IN)
unnamed: R903.2, U903.6 (FLAG1)

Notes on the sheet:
ADC Power Supply
ADC SPI Bus
ADC GPIO
ADC Analog Inputs
Signal Conditioning
Voltage Reference
Power Sequencer
All "special" channels have option to convert to standard (0-5V) mode
LPF values recommended by TI
3.3V Linear Regulator
SPI signal decoder: S0 = CS S1 = SCLK S2 = MISO S3 = MOSI

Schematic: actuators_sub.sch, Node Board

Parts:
C1502, C1505, C1507, C1508, C1509, C1510, C1512, C1513, C1515, C1516: 0.1uF; C_0805_HandSoldering
C1503, C1506: 100uF; C_0805_HandSoldering
C1511, C1514: NOSTUFF; C_0805_HandSoldering
J1501, J1502, J1503, J1504, J1505, J1506, J1507, J1508: CONN_01X02; Molex_2pin_power_0010844022; MFG. P/N 0010844022
J1509, J1510: CONN_01X04; Molex_4pin_power_10-84-4042; MFG. P/N 10-84-4042
R1501, R1506: 10k; R_0805_HandSoldering
R1502, R1503, R1504, R1505, R1507, R1508, R2001, R2103, R2105, R2106, R2108, R2109, R2110, R2111, R2112: 0; R_0805_HandSoldering
R2002: 150; R_0805_HandSoldering
R2003, R2004: 15k; R_0805_HandSoldering
TP2001: Conn_01x01; Testpoint_circle_0.5mm
TP2101, TP2102: CONN_01X01; Testpoint_circle_0.5mm
U1501, U1502: DRV8806; TSSOP-16-1EP_4.4x5mm_Pitch0.65mm; Mfg. Part Num DRV8806PWPR
U1503, U1504: DAC7760; HTSSOP-24_7.8x4.4mm_Pitch0.65mm_ThermalPad; Manufacturer P/N DAC7760IPWPR
U1505, U1506: OPA172; SOT-23-5; MFG. P/N OPA172IDBVR
U2001: BTS4300SGA; SOIC-8_3.9x4.9mm_Pitch1.27mm; Mfg. Part Num BTS4300SGAXUMA1

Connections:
+3V3: C1512.2, C1515.2, R1501.1, R1506.1, R2003.1, R2004.1, U1503.2 (DVDD), U1504.2 (DVDD); also elsewhere on the board
+24V: C1502.2, C1503.2, C1505.2, C1506.2, J1501.1, J1502.1, J1503.1, J1504.1, J1505.1, J1506.1, J1507.1, J1508.1, J1509.1, J1510.1, R2001.2, U1501.1 (VM), U1501.2 (VCLAMP), U1502.1 (VM), U1502.2 (VCLAMP), U2001.5 (IN), U2001.6 (IN), U2001.7 (IN), U2001.8 (IN); also elsewhere on the board
/Actuator Interface/24V0_DAC: C1507.2, C1508.2, C1509.2, C1510.2, R2001.1, U1503.24 (AVDD), U1504.24 (AVDD), U1505.5, U1506.5, U2001.3 (OUT)
/Actuator Interface/DAC1_CLR_SEL: R1504.2, U1503.6 (CLR)
/Actuator Interface/DAC1_DATAIN: R2103.2, U1503.9 (DIN)
/Actuator Interface/DAC1_DATAOUT: U1503.10 (SDO), U1504.9 (DIN)
/Actuator Interface/DAC1_DVDD_EN_L: R1505.2, U1503.16 (DVDD-EN)
/Actuator Interface/DAC1_VIOUT: C1514.1, J1509.2, R1508.1, U1503.19 (IOUT), U1503.21 (VOUT), U1505.3; also elsewhere on the board
/Actuator Interface/DAC1_VREF: C1516.2, U1503.14 (REFOUT), U1503.15 (REFIN)
/Actuator Interface/DAC1_VSENSE+: R1508.2, U1503.22 (+VSENSE), U1505.1, U1505.4
/Actuator Interface/DAC2_CLR_SEL: R1502.2, U1504.6 (CLR)
/Actuator Interface/DAC2_DATAOUT: R2108.2, U1504.10 (SDO)
/Actuator Interface/DAC2_DVDD_EN_L: R1503.2, U1504.16 (DVDD-EN)
/Actuator Interface/DAC2_VIOUT: C1511.1, J1510.2, R1507.1, U1504.19 (IOUT), U1504.21 (VOUT), U1506.3; also elsewhere on the board
/Actuator Interface/DAC2_VREF: C1513.2, U1504.14 (REFOUT), U1504.15 (REFIN)
/Actuator Interface/DAC2_VSENSE+: R1507.2, U1504.22 (+VSENSE), U1506.1, U1506.4
/Actuator Interface/DAC_ALARM_L: R1506.2, U1503.3 (~ALARM), U1504.3 (~ALARM); also elsewhere on the board
/Actuator Interface/DAC_CLR: U1503.5 (CLR-SEL), U1504.5 (CLR-SEL); also elsewhere on the board
/Actuator Interface/DAC_CS: R2105.2, U1503.7 (LATCH), U1504.7 (LATCH)
/Actuator Interface/DAC_SCLK: R2106.2, U1503.8 (SCLK), U1504.8 (SCLK)
/Actuator Interface/Q0: R2109.1, R2109.2, U1501.11 (LATCH(CS)), U1502.11 (LATCH(CS)); also elsewhere on the board
/Actuator Interface/Q1: R2110.1; also elsewhere on the board
/Actuator Interface/Q2: R2111.1; also elsewhere on the board
/Actuator Interface/Q3: R2112.1; also elsewhere on the board
/Actuator Interface/SOL1_DATAIN: R2111.2, U1501.14 (SDATIN)
/Actuator Interface/SOL1_DATAOUT: U1501.15 (SDATOUT), U1502.14 (SDATIN)
/Actuator Interface/SOL1_OUT1: J1501.2, U1501.3 (OUT1)
/Actuator Interface/SOL1_OUT2: J1502.2, U1501.4 (OUT2)
/Actuator Interface/SOL1_OUT3: J1503.2, U1501.6 (OUT3)
/Actuator Interface/SOL1_OUT4: J1504.2, U1501.7 (OUT4)
/Actuator Interface/SOL1_RST: TP2102.1, U1501.9 (RESET)
/Actuator Interface/SOL2_DATAOUT: R2112.2, U1502.15 (SDATOUT)
/Actuator Interface/SOL2_OUT1: J1505.2, U1502.3 (OUT1)
/Actuator Interface/SOL2_OUT2: J1506.2, U1502.4 (OUT2)
/Actuator Interface/SOL2_OUT3: J1507.2, U1502.6 (OUT3)
/Actuator Interface/SOL2_OUT4: J1508.2, U1502.7 (OUT4)
/Actuator Interface/SOL2_RST: TP2101.1, U1502.9 (RESET)
/Actuator Interface/SOL_DAC_C0: R1501.2, U1501.16 (~FAULT), U1502.16 (~FAULT); also elsewhere on the board
/Actuator Interface/SOL_DAC_C1: U1501.8 (~ENBL), U1502.8 (~ENBL); also elsewhere on the board
/Actuator Interface/SOL_DAC_CS2: R2105.1; also elsewhere on the board
/Actuator Interface/SOL_DAC_MISO: R2108.1; also elsewhere on the board
/Actuator Interface/SOL_DAC_MOSI: R2103.1; also elsewhere on the board
/Actuator Interface/SOL_DAC_S1: R2106.1; also elsewhere on the board
/Actuator Interface/SOL_SCLK: R2110.2, U1501.13 (SCLK), U1502.13 (SCLK)
/Microcontroller/PB02: R2003.2, U2001.2 (EN); also elsewhere on the board
/Microcontroller/PB03: R2004.2, TP2001.1, U2001.4 (STATUS); also elsewhere on the board
GND: C1502.1, C1503.1, C1505.1, C1506.1, C1507.1, C1508.1, C1509.1, C1510.1, C1512.1, C1513.1, C1515.1, C1516.1, J1509.3, J1509.4, J1510.3, J1510.4, R1502.1, R1503.1, R1504.1, R1505.1, R2002.2, U1501.5 (GND), U1501.12 (GND), U1501.17 (THRM), U1502.5 (GND), U1502.12 (GND), U1502.17 (THRM), U1503.1 (AVSS), U1503.4 (DGND), U1503.11 (AGND), U1503.12 (AGND), U1503.23 (-VSENSE), U1504.1 (AVSS), U1504.4 (DGND), U1504.11 (AGND), U1504.12 (AGND), U1504.23 (-VSENSE), U1505.2, U1506.2; also elsewhere on the board
unnamed: C1511.2, U1504.17 (CMP)
unnamed: C1514.2, U1503.17 (CMP)
unnamed: R2002.1, U2001.1 (GND)

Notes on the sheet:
Solenoid Controller 1
Digital-to-Analog Converter (DAC) 1
Solenoid Controller 2
Solenoid/Valve Bus Connections
DAC Power Supply Sequencer
Digital-to-Analog Converter (DAC) 2
SPI signal decoder: S0 = CS S1 = SCLK S2 = MISO S3 = MOSI S4 = CS2
Solenoid/DAC control signal decoder: S0 = SOL_FAULT S1 = SOL_ENBL S2 = DAC_CLR S3 = DAC_ALARM
For solenoid only, leave the following unstuffed: R2105 R2106 R2107 R2108 For combined, unstuff R2104
Reverse current limiting
Optional bypass

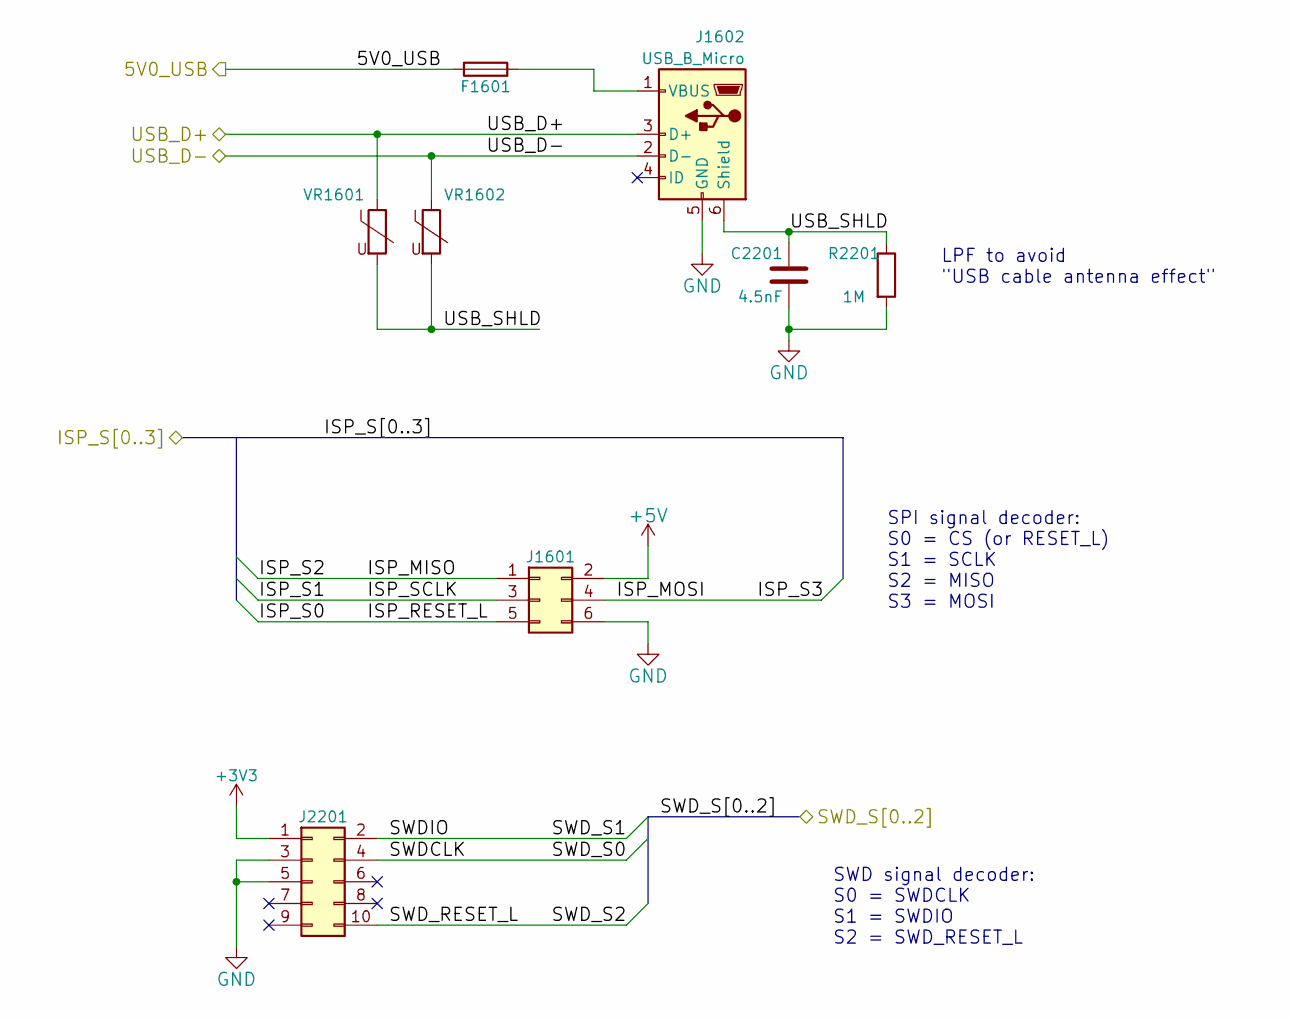
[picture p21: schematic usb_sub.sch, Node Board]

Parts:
C2201: 4.5nF; C_0805_HandSoldering
F1601: Fuse; R_1812_HandSoldering; Mfg. Part Num MF-MSMF050-2CT-ND
J1601: Conn_02x03_Odd_Even; Pin_Header_Straight_2x03_Pitch2.54mm; MFG. P/N GRPB032VWVN-RC
J1602: USB_B_Micro; USB_Micro-B_10103594-0001LF; Mfg. Part Num 609-4050-1-ND
J2201: Conn_02x05_Odd_Even; Pin_Header_Straight_2x05_Pitch1.27mm; MFG. P/N 20021111-00010T4LF
R2201: 1M; R_0805_HandSoldering
VR1601, VR1602: VR; R_0603_HandSoldering; Mfg. Part Num CG0603MLC-05E

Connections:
+3V3: J2201.1; also elsewhere on the board
+5V: J1601.2; also elsewhere on the board
/Microcontroller/ISP_MISO: J1601.1; also elsewhere on the board
/Microcontroller/ISP_MOSI: J1601.4; also elsewhere on the board
/Microcontroller/ISP_RESET_L: J1601.5; also elsewhere on the board
/Microcontroller/ISP_S1: J1601.3; also elsewhere on the board
/Microcontroller/SWDCLK: J2201.4; also elsewhere on the board
/Microcontroller/SWDIO: J2201.2; also elsewhere on the board
/Microcontroller/SWD_RESET_L: J2201.10; also elsewhere on the board
/Microcontroller/USB_D+: J1602.3 (D+), VR1601.1; also elsewhere on the board
/Microcontroller/USB_D-: J1602.2 (D-), VR1602.1; also elsewhere on the board
/Power/5V0_USB: F1601.2; also elsewhere on the board
/USB Interface/USB_SHLD: C2201.1, J1602.6 (Shield), R2201.1, VR1601.2, VR1602.2
GND: C2201.2, J1601.6, J1602.5 (GND), J2201.3, J2201.5, R2201.2; also elsewhere on the board
unnamed: F1601.1, J1602.1 (VBUS)

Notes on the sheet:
LPF to avoid "USB cable antenna effect"
SPI signal decoder: S0 = CS (or RESET_L) S1 = SCLK S2 = MISO S3 = MOSI
SWD signal decoder: S0 = SWDCLK S1 = SWDIO S2 = SWD_RESET_L

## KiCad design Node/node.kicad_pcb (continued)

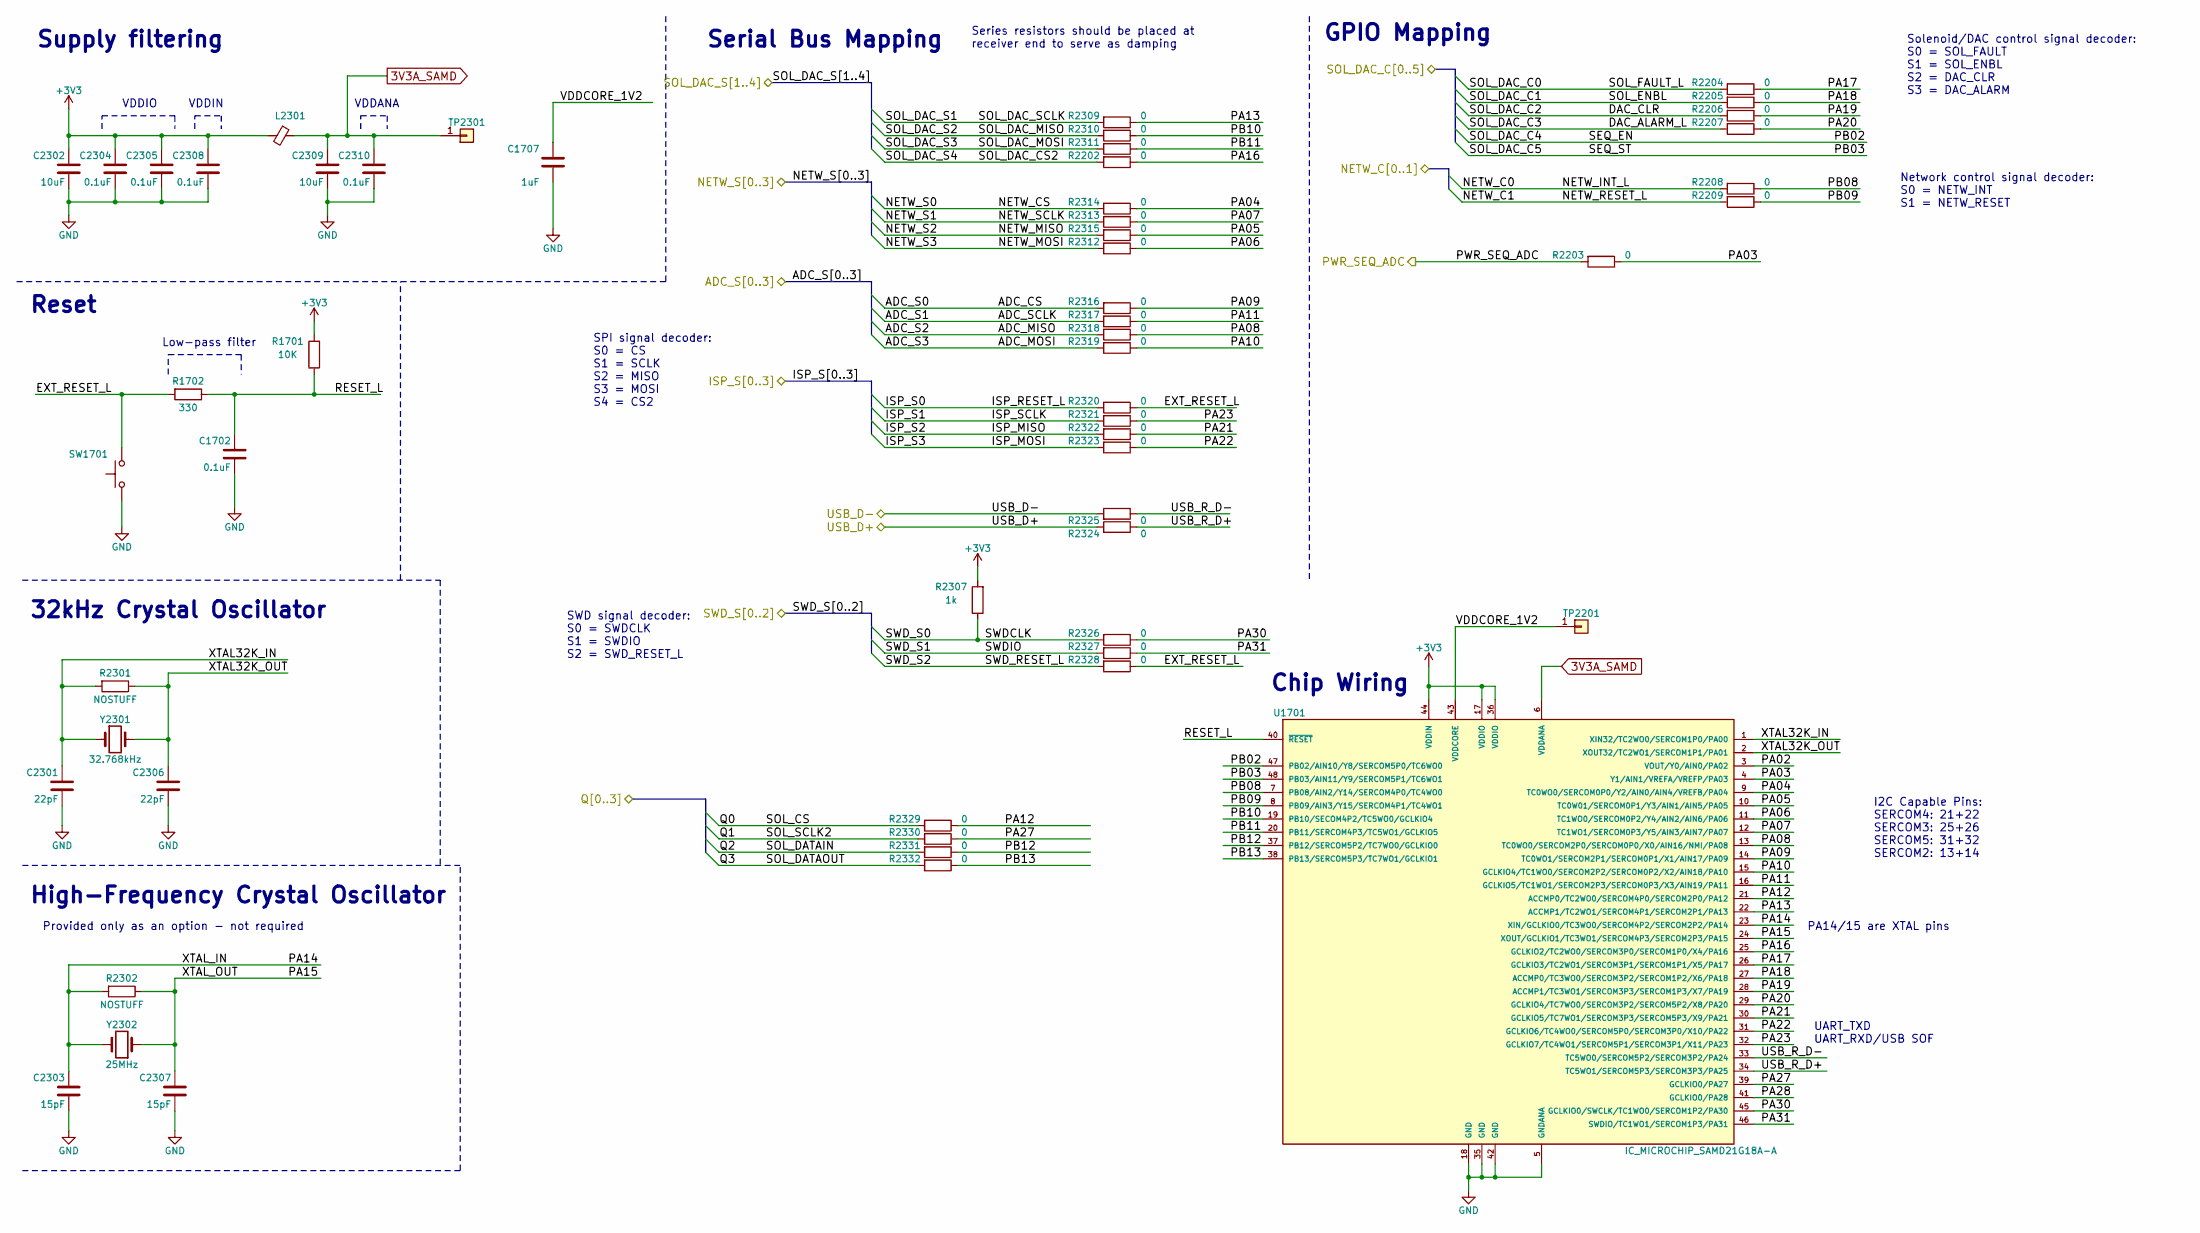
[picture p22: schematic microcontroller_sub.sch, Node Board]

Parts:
C1702, C2304, C2305, C2308, C2310: 0.1uF; C_0805_HandSoldering
C1707: 1uF; C_0805_HandSoldering
C2301, C2306: 22pF; C_0805_HandSoldering
C2302, C2309: 10uF; C_0805_HandSoldering
C2303, C2307: 15pF; C_0805_HandSoldering
L2301: Ferrite_Bead_Small; R_1206_HandSoldering
R1701: 10K; R_0805_HandSoldering
R1702: 330; R_0805_HandSoldering
R2202, R2203, R2204, R2205, R2206, R2207, R2208, R2209, R2309, R2310, R2311, R2312, R2313, R2314, R2315, R2316, R2317, R2318, R2319, R2320, R2321, R2322, R2323, R2324, R2325, R2326, R2327, R2328, R2329, R2330, R2331, R2332: 0; R_0805_HandSoldering
R2301, R2302: NOSTUFF; R_0805_HandSoldering
R2307: 1k; R_0805_HandSoldering
SW1701: SW_Push; C&K_switch_PTS645SM43SMTR92; MFG. P/N PTS645SM43SMTR92 LFS
TP2201, TP2301: Conn_01x01; Testpoint_circle_0.5mm
U1701: IC_MICROCHIP_SAMD21G18A-A; TQFP-48_7x7mm_Pitch0.5mm; MFG. P/N ATSAMD21G18A-AUT
Y2301: 32.768kHz; TXC_32kHz_XTAL_9HT10-32.768KBZY-T; Mfg. Part Num 9HT10-32.768KBZY-T
Y2302: 25MHz; Murata_25MHz_XTAL_XRCGB25M000F3M00R0; Mfg. Part Num XRCGB25M000F3M00R0

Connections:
3V3A_SAMD: C2309.1, C2310.1, L2301.1, TP2301.1, U1701.6 (VDDANA)
+3V3: C2302.1, C2304.1, C2305.1, C2308.1, L2301.2, R1701.2, R2307.2, U1701.17 (VDDIO), U1701.36 (VDDIO), U1701.44 (VDDIN); also elsewhere on the board
/Actuator Interface/DAC_ALARM_L: R2207.2; also elsewhere on the board
/Actuator Interface/DAC_CLR: R2206.2; also elsewhere on the board
/Actuator Interface/Q0: R2329.2; also elsewhere on the board
/Actuator Interface/Q1: R2330.2; also elsewhere on the board
/Actuator Interface/Q2: R2331.2; also elsewhere on the board
/Actuator Interface/Q3: R2332.2; also elsewhere on the board
/Actuator Interface/SOL_DAC_C0: R2204.2; also elsewhere on the board
/Actuator Interface/SOL_DAC_C1: R2205.2; also elsewhere on the board
/Actuator Interface/SOL_DAC_CS2: R2202.2; also elsewhere on the board
/Actuator Interface/SOL_DAC_MISO: R2310.2; also elsewhere on the board
/Actuator Interface/SOL_DAC_MOSI: R2311.2; also elsewhere on the board
/Actuator Interface/SOL_DAC_S1: R2309.2; also elsewhere on the board
/Microcontroller/ADC_CS: R2316.2; also elsewhere on the board
/Microcontroller/ADC_MISO: R2318.2; also elsewhere on the board
/Microcontroller/ADC_MOSI: R2319.2; also elsewhere on the board
/Microcontroller/ADC_S1: R2317.2; also elsewhere on the board
/Microcontroller/EXT_RESET_L: R1702.2, R2320.1, R2328.1, SW1701.2
/Microcontroller/ISP_MISO: R2322.2; also elsewhere on the board
/Microcontroller/ISP_MOSI: R2323.2; also elsewhere on the board
/Microcontroller/ISP_RESET_L: R2320.2; also elsewhere on the board
/Microcontroller/ISP_S1: R2321.2; also elsewhere on the board
/Microcontroller/NETW_C0: R2208.2; also elsewhere on the board
/Microcontroller/NETW_C1: R2209.2; also elsewhere on the board
/Microcontroller/NETW_CS: R2314.2; also elsewhere on the board
/Microcontroller/NETW_MISO: R2315.2; also elsewhere on the board
/Microcontroller/NETW_MOSI: R2312.2; also elsewhere on the board
/Microcontroller/NETW_S1: R2313.2; also elsewhere on the board
/Microcontroller/PA02: U1701.3 (VOUT/Y0/AIN0/PA02)
/Microcontroller/PA03: R2203.1, U1701.4 (Y1/AIN1/VREFA/VREFP/PA03)
/Microcontroller/PA04: R2314.1, U1701.9 (TC0WO0/SERCOM0P0/Y2/AIN0/AIN4/VREFB/PA04)
/Microcontroller/PA05: R2315.1, U1701.10 (TC0W01/SERCOM0P1/Y3/AIN1/AIN5/PA05)
/Microcontroller/PA06: R2312.1, U1701.11 (TC1WO0/SERCOM0P2/Y4/AIN2/AIN6/PA06)
/Microcontroller/PA07: R2313.1, U1701.12 (TC1WO1/SERCOM0P3/Y5/AIN3/AIN7/PA07)
/Microcontroller/PA08: R2318.1, U1701.13 (TC0WO0/SERCOM2P0/SERCOM0P0/X0/AIN16/NMI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)
/Microcontroller/PA09: R2316.1, U1701.14 (TC0WO1/SERCOM2P1/SERCOM0P1/X1/AIN17/PA09)
/Microcontroller/PA10: R2319.1, U1701.15 (GCLKIO4/TC1WO0/SERCOM2P2/SERCOM0P2/X2/A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)
/Microcontroller/PA11: R2317.1, U1701.16 (GCLKIO5/TC1WO1/SERCOM2P3/SERCOM0P3/X3/A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)
/Microcontroller/PA12: R2329.1, U1701.21 (ACCMP0/TC2WO0/SERCOM4P0/SERCOM2P0/PA12)
/Microcontroller/PA13: R2309.1, U1701.22 (ACCMP1/TC2WO1/SERCOM4P1/SERCOM2P1/PA13)
/Microcontroller/PA14: C2303.1, R2302.2, U1701.23 (XIN/GCLKIO0/TC3WO0/SERCOM4P2/SERCOM2P2/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), Y2302.2
/Microcontroller/PA15: C2307.1, R2302.1, U1701.24 (XOUT/GCLKIO1/TC3WO1/SERCOM4P3/SERCOM2P3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), Y2302.1
/Microcontroller/PA16: R2202.1, U1701.25 (GCLKIO2/TC2WO0/SERCOM3P0/SERCOM1P0/X4/P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)
/Microcontroller/PA17: R2204.1, U1701.26 (GCLKIO3/TC2WO1/SERCOM3P1/SERCOM1P1/X5/P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)
/Microcontroller/PA18: R2205.1, U1701.27 (ACCMP0/TC3WO0/SERCOM3P2/SERCOM1P2/X6/PA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)
/Microcontroller/PA19: R2206.1, U1701.28 (ACCMP1/TC3WO1/SERCOM3P3/SERCOM1P3/X7/PA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)
/Microcontroller/PA20: R2207.1, U1701.29 (GCLKIO4/TC7WO0/SERCOM3P2/SERCOM5P2/X8/P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)
/Microcontroller/PA21: R2322.1, U1701.30 (GCLKIO5/TC7WO1/SERCOM3P3/SERCOM5P3/X9/P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)
/Microcontroller/PA22: R2323.1, U1701.31 (GCLKIO6/TC4WO0/SERCOM5P0/SERCOM3P0/X10/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)
/Microcontroller/PA23: R2321.1, U1701.32 (GCLKIO7/TC4WO1/SERCOM5P1/SERCOM3P1/X11/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)
/Microcontroller/PA27: R2330.1, U1701.39 (GCLKIO0/PA27)
/Microcontroller/PA28: U1701.41 (GCLKIO0/PA28)
/Microcontroller/PA30: R2326.1, U1701.45 (GCLKIO0/SWCLK/TC1WO0/SERCOM1P2/PA30)
/Microcontroller/PA31: R2327.1, U1701.46 (SWDIO/TC1WO1/SERCOM1P3/PA31)
/Microcontroller/PB02: U1701.47 (PB02/AIN10/Y8/SERCOM5P0/TC6WO0); also elsewhere on the board
/Microcontroller/PB03: U1701.48 (PB03/AIN11/Y9/SERCOM5P1/TC6WO1); also elsewhere on the board
/Microcontroller/PB08: R2208.1, U1701.7 (PB08/AIN2/Y14/SERCOM4P0/TC4WO0)
/Microcontroller/PB09: R2209.1, U1701.8 (PB09/AIN3/Y15/SERCOM4P1/TC4WO1)
/Microcontroller/PB10: R2310.1, U1701.19 (PB10/SECOM4P2/TC5WO0/GCLKIO4)
/Microcontroller/PB11: R2311.1, U1701.20 (PB11/SERCOM4P3/TC5WO1/GCLKIO5)
/Microcontroller/PB12: R2331.1, U1701.37 (PB12/SERCOM5P2/TC7WO0/GCLKIO0)
/Microcontroller/PB13: R2332.1, U1701.38 (PB13/SERCOM5P3/TC7WO1/GCLKIO1)
/Microcontroller/RESET_L: C1702.1, R1701.1, R1702.1, U1701.40 (~RESET~)
/Microcontroller/SWDCLK: R2307.1, R2326.2; also elsewhere on the board
/Microcontroller/SWDIO: R2327.2; also elsewhere on the board
/Microcontroller/SWD_RESET_L: R2328.2; also elsewhere on the board
/Microcontroller/USB_D+: R2324.2; also elsewhere on the board
/Microcontroller/USB_D-: R2325.2; also elsewhere on the board
/Microcontroller/USB_R_D+: R2324.1, U1701.34 (TC5WO1/SERCOM5P3/SERCOM3P3/PA25)
/Microcontroller/USB_R_D-: R2325.1, U1701.33 (TC5WO0/SERCOM5P2/SERCOM3P2/PA24)
/Microcontroller/VDDCORE_1V2: C1707.2, TP2201.1, U1701.43 (VDDCORE)
/Microcontroller/XTAL32K_IN: C2301.1, R2301.2, U1701.1 (XIN32/TC2WO0/SERCOM1P0/PA00), Y2301.1
/Microcontroller/XTAL32K_OUT: C2306.1, R2301.1, U1701.2 (XOUT32/TC2WO1/SERCOM1P1/PA01), Y2301.2
/Sensors/ADC/POWER_SEQ_ADC: R2203.2; also elsewhere on the board
GND: C1702.2, C1707.1, C2301.2, C2302.2, C2303.2, C2304.2, C2305.2, C2306.2, C2307.2, C2308.2, C2309.2, C2310.2, SW1701.1, U1701.5 (GNDANA), U1701.18 (GND), U1701.35 (GND), U1701.42 (GND); also elsewhere on the board

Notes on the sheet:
I2C Capable Pins: SERCOM4: 21+22 SERCOM3: 25+26 SERCOM5: 31+32 SERCOM2: 13+14
Supply filtering
Reset
Low-pass filter
Chip Wiring
GPIO Mapping
Serial Bus Mapping
Series resistors should be placed at receiver end to serve as damping
UART_TXD UART_RXD/USB SOF
32kHz Crystal Oscillator
VDDIN
VDDIO
VDDANA
High-Frequency Crystal Oscillator
Provided only as an option - not required
PA14/15 are XTAL pins
SWD signal decoder: S0 = SWDCLK S1 = SWDIO S2 = SWD_RESET_L
SPI signal decoder: S0 = CS S1 = SCLK S2 = MISO S3 = MOSI S4 = CS2
Solenoid/DAC control signal decoder: S0 = SOL_FAULT S1 = SOL_ENBL S2 = DAC_CLR S3 = DAC_ALARM
Network control signal decoder: S0 = NETW_INT S1 = NETW_RESET

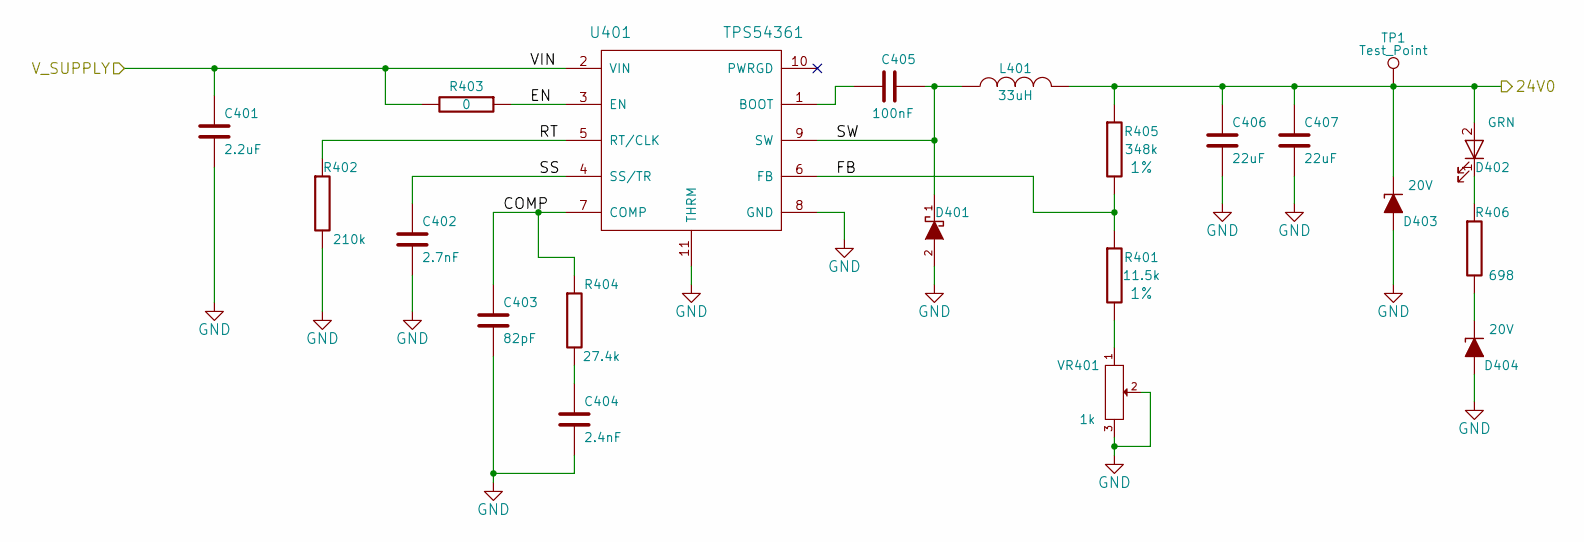
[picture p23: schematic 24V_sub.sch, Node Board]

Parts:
C401: 2.2uF; C_1206_HandSoldering; Mfg. Part Num C3216X7S2A225K160AB
C402: 2.7nF; C_0805_HandSoldering; Mfg. Part Num CC0805KRX7R9BB272
C403: 82pF; C_0805_HandSoldering; Mfg. Part Num CL21C820JB61PNC
C404: 2.4nF; C_0805_HandSoldering; Mfg. Part Num GRM2165C1H242JA01D
C405: 100nF; C_0805_HandSoldering; Mfg. Part Num GMK212BJ104KGHT
C406, C407: 22uF; C_0805_HandSoldering; Mfg. Part Num C2012X5R1V226M125AC
D401: DIODESCH; D_SMC_Handsoldering; Mfg. Part Num B560C-13-F
D402: GRN; LED_1206_HandSoldering; Mfg. Part Num APT3216LZGCK
D403, D404: 20V; D_SOD-323_HandSoldering; Mfg. Part Num MM3Z20VT1G
L401: 33uH; Wurth_inductor_7443551331; Mfg. Part Num 7443551331
R401: 11.5k; R_0805_HandSoldering; Tolerance 1%; MFG. P/N RC0805FR-0711K5L
R402: 210k; R_0805_HandSoldering; Mfg. Part Num ERA-6AEB2103V
R403: 0; R_0805_HandSoldering; Mfg. Part Num ERJ-6GEY0R00V
R404: 27.4k; R_0805_HandSoldering; Mfg. Part Num RC0805FR-0727K4L
R405: 348k; R_0805_HandSoldering; Tolerance 1%; MFG. P/N RC0805FR-07348KL
R406: 698; R_0805_HandSoldering; Mfg. Part Num RC0805FR-07698RL
TP1: Test_Point; Test_Point_Keystone_5000-5004_Miniature; Manufacturer P/N 5000
U401: TPS54361; TI_buckreg_TPS54361DPRR; Mfg. Part Num TPS54361DPRR
VR401: 1k; TT_1k_potentiometer_23BR1KLFTR; Mfg. Part Num 23BR1KLFTR

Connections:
+24V: C406.1, C407.1, D402.2 (A), D403.1 (K), L401.2, R405.1, TP1.1; also elsewhere on the board
/Power/ISENSE_N: C401.1, R403.2, U401.2 (VIN); also elsewhere on the board
/Power/Motor Supply/COMP: C403.1, R404.1, U401.7 (COMP)
/Power/Motor Supply/EN: R403.1, U401.3 (EN)
/Power/Motor Supply/FB: R401.1, R405.2, U401.6 (FB)
/Power/Motor Supply/RT: R402.1, U401.5 (RT/CLK)
/Power/Motor Supply/SS: C402.1, U401.4 (SS/TR)
/Power/Motor Supply/SW: C405.1, D401.1 (A), L401.1, U401.9 (SW)
GND: C401.2, C402.2, C403.2, C404.2, C406.2, C407.2, D401.2 (K), D403.2 (A), D404.2 (A), R402.2, U401.8 (GND), U401.11 (THRM), VR401.2, VR401.3; also elsewhere on the board
unnamed: C404.1, R404.2
unnamed: C405.2, U401.1 (BOOT)
unnamed: D402.1 (K), R406.1
unnamed: D404.1 (K), R406.2
unnamed: R401.2, VR401.1

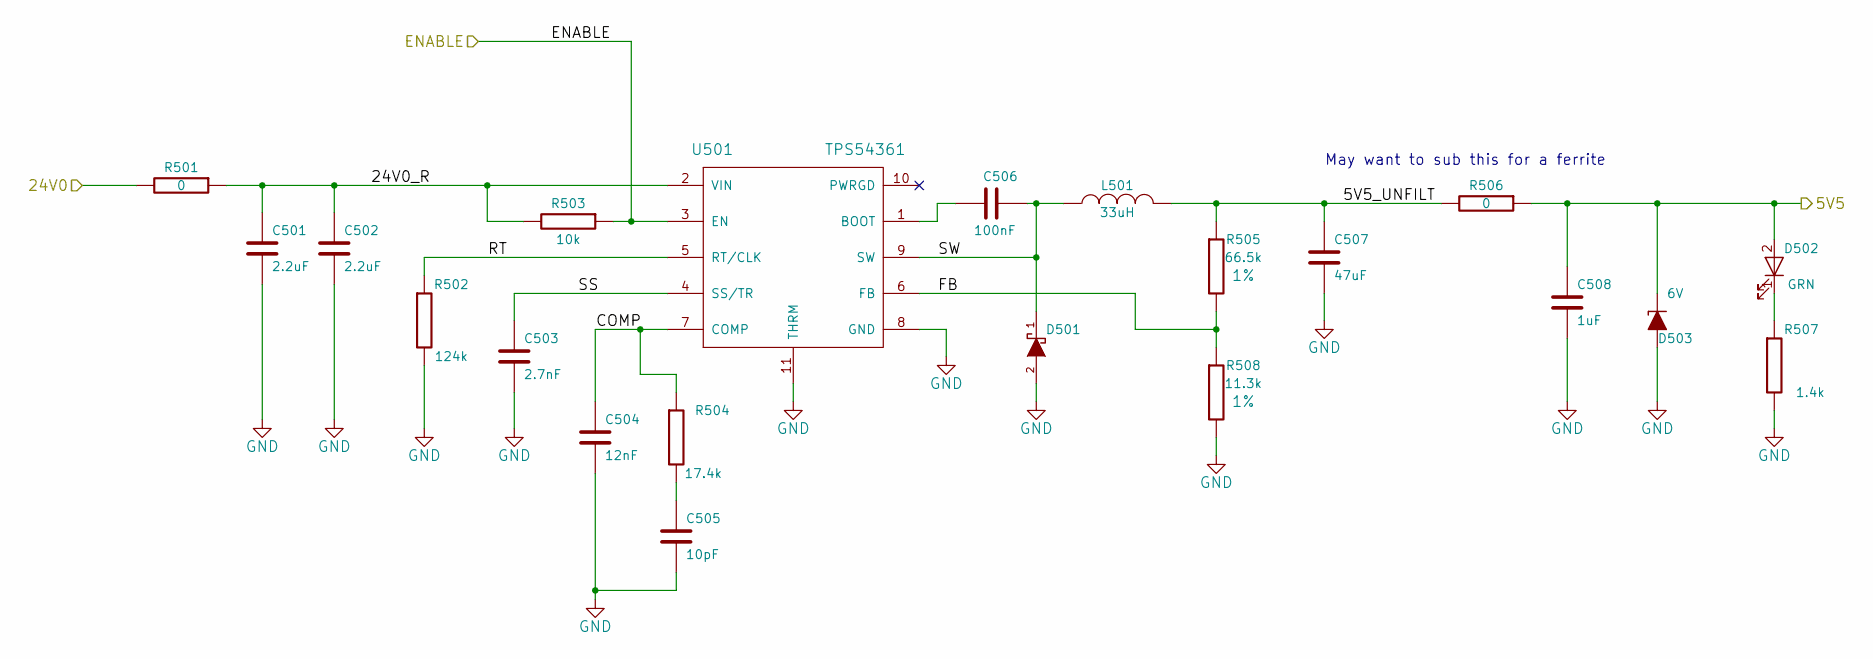
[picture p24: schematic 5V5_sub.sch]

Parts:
C501, C502: 2.2uF; C_0805_HandSoldering; Mfg. Part Num C2012X7R1H225K125AC
C503: 2.7nF; C_0805_HandSoldering; Mfg. Part Num CC0805KRX7R9BB272
C504: 12nF; C_0805_HandSoldering; Mfg. Part Num CL21B123KBANNNC
C505: 10pF; C_0805_HandSoldering; Mfg. Part Num C0805C100K5GACTU
C506: 100nF; C_0805_HandSoldering; Mfg. Part Num GMK212BJ104KGHT
C507: 47uF; C_1206_HandSoldering; Mfg. Part Num CL31A476MPHNNNE
C508: 1uF; C_0805_HandSoldering
D501: DIODESCH; D_SMB_Handsoldering; Mfg. Part Num B140B-13-F
D502: GRN; LED_1206_HandSoldering; Mfg. Part Num APT3216LZGCK
D503: 6V; D_SOD-123; Mfg. Part Num MMSZ5233B-TP
L501: 33uH; Bourns_33uH_inductor_SRR6028-330Y; Mfg. Part Num SRR6028-330Y
R501, R506: 0; R_0805_HandSoldering; Mfg. Part Num RC0805JR-070RL
R502: 124k; R_0805_HandSoldering; Mfg. Part Num RC0805FR-07124KL
R503: 10k; R_0805_HandSoldering
R504: 17.4k; R_0805_HandSoldering; Mfg. Part Num RC0805FR-0717K4L
R505: 66.5k; R_0805_HandSoldering; Tolerance 1%; Mfg. Part Num ERJ-6ENF6652V
R507: 1.4k; R_0805_HandSoldering; Mfg. Part Num RC0805FR-071K4L
R508: 11.3k; R_0805_HandSoldering; Tolerance 1%
U501: TPS54361; TI_buckreg_TPS54361DPRR; Mfg. Part Num TPS54361DPRR

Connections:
+24V: R501.2; also elsewhere on the board
/Power/3.3V (Clean) Supply/5V5: C508.1, D502.2 (A), D503.1 (K), R506.1; also elsewhere on the board
/Power/5.5V (Noisy) Supply/5V5_UNFILT: C507.1, L501.2, R505.1, R506.2
/Power/5.5V (Noisy) Supply/24V0_R: C501.1, C502.1, R501.1, R503.2, U501.2 (VIN)
/Power/5.5V (Noisy) Supply/COMP: C504.1, R504.1, U501.7 (COMP)
/Power/5.5V (Noisy) Supply/ENABLE: R503.1, U501.3 (EN); also elsewhere on the board
/Power/5.5V (Noisy) Supply/FB: R505.2, R508.1, U501.6 (FB)
/Power/5.5V (Noisy) Supply/RT: R502.1, U501.5 (RT/CLK)
/Power/5.5V (Noisy) Supply/SS: C503.1, U501.4 (SS/TR)
/Power/5.5V (Noisy) Supply/SW: C506.1, D501.1 (A), L501.1, U501.9 (SW)
GND: C501.2, C502.2, C503.2, C504.2, C505.2, C507.2, C508.2, D501.2 (K), D503.2 (A), R502.2, R507.2, R508.2, U501.8 (GND), U501.11 (THRM); also elsewhere on the board
unnamed: C505.1, R504.2
unnamed: C506.2, U501.1 (BOOT)
unnamed: D502.1 (K), R507.1

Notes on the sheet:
May want to sub this for a ferrite

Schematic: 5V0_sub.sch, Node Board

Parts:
C601: 1uF; C_0805_HandSoldering; Mfg. Part Num GRT21BC81E105KE13L
C602: 15pF; C_0805_HandSoldering; Mfg. Part Num CC0805JRNPO9BN150
C603: 1uF; C_0805_HandSoldering; Mfg. Part Num CC0805KRX5R7BB105
C604: C; C_0805_HandSoldering
D601: GRN; LED_1206_HandSoldering; Mfg. Part Num APT3216LZGCK
D602: 6V; D_SOD-123; Mfg. Part Num MMSZ5233B-TP
L601: INDUCTOR_SMALL; R_1206_HandSoldering; Mfg. Part Num RC1206JR-070RL
R601: 10k; R_0805_HandSoldering
R602: 93.1k; R_0805_HandSoldering; Tolerance 1%; MFG. P/N RC0805FR-0793K1L
R603: 29.4k; R_0805_HandSoldering; Tolerance 1%
R604: 1.2k; R_0805_HandSoldering; Mfg. Part Num RC0805JR-071K2L
TP3: Test_Point; Test_Point_Keystone_5000-5004_Miniature; Manufacturer P/N 5000
U601: TPS795; SOT-223-6; Mfg. Part Num TPS79501DCQR
VR601: 1k; TT_1k_potentiometer_23BR1KLFTR; Mfg. Part Num 23BR1KLFTR

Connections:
+5V: C604.1, D601.2 (A), D602.1 (K), L601.2, TP3.1; also elsewhere on the board
/Power/3.3V (Clean) Supply/5V5: C601.1, R601.1, U601.2 (IN); also elsewhere on the board
/Power/5V (Clean) Supply/5V0_UNFILT: C602.1, C603.1, L601.1, R602.1, U601.4 (OUT)
/Power/5V (Clean) Supply/ENABLE: R601.2, U601.1 (EN); also elsewhere on the board
GND: C601.2, C603.2, C604.2, D602.2 (A), R604.2, U601.3 (GND), U601.6 (THRM), VR601.2, VR601.3; also elsewhere on the board
unnamed: C602.2, R602.2, R603.1, U601.5 (FB)
unnamed: D601.1 (K), R604.1
unnamed: R603.2, VR601.1

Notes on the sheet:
Low pass filter
Stuff ferrite with 0Ω if no filter is required

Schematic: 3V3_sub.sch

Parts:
C701: 1uF; C_0805_HandSoldering; Mfg. Part Num GRT21BC81E105KE13L
C702: 15pF; C_0805_HandSoldering; Mfg. Part Num CC0805JRNPO9BN150
C703: 1uF; C_0805_HandSoldering; Mfg. Part Num CC0805KRX5R7BB105
C704: C; C_0805_HandSoldering
D701: GRN; LED_1206_HandSoldering; Mfg. Part Num APT3216LZGCK
D702: 3.6V; D_SOD-323_HandSoldering; Mfg. Part Num MM3Z3V6T1G
L701: INDUCTOR_SMALL; R_1206_HandSoldering; Mfg. Part Num RC1206JR-070RL
R701: 10k; R_0805_HandSoldering
R702: 51k; R_0805_HandSoldering; Mfg. Part Num RC0805FR-0751KL
R703: 29.4k; R_0805_HandSoldering; Tolerance 1%
R704: 330; R_0805_HandSoldering; Mfg. Part Num RC0805JR-07330RL
U701: TPS795; SOT-223-6; Mfg. Part Num TPS79501DCQR
VR701: 1k; TT_1k_potentiometer_23BR1KLFTR; Mfg. Part Num 23BR1KLFTR

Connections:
+3V3: C704.1, D701.2 (A), D702.1 (K), L701.2; also elsewhere on the board
/Power/3.3V (Clean) Supply/3V3_UNFILT: C702.1, C703.1, L701.1, R702.1, U701.4 (OUT)
/Power/3.3V (Clean) Supply/5V5: C701.1, R701.1, U701.2 (IN); also elsewhere on the board
GND: C701.2, C703.2, C704.2, D702.2 (A), R704.2, U701.3 (GND), U701.6 (THRM), VR701.2, VR701.3; also elsewhere on the board
unnamed: C702.2, R702.2, R703.1, U701.5 (FB)
unnamed: D701.1 (K), R704.1
unnamed: R701.2, U701.1 (EN)
unnamed: R703.2, VR701.1

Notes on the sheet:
Low pass filter
Stuff ferrite with 0Ω if no filter is required

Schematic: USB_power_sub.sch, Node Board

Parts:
J801: Conn_02x02_Odd_Even; Pin_Header_Straight_2x02_Pitch2.54mm; MFG. P/N 67997-404HLF
J802, J803: Conn_02x01; Pin_Header_Straight_2x01_Pitch2.54mm; MFG. P/N M20-9990246
TP5: Test_Point; Test_Point_Keystone_5000-5004_Miniature; Manufacturer P/N 5000

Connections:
+5V: J801.2; also elsewhere on the board
/Power/3.3V (Clean) Supply/5V5: J801.4; also elsewhere on the board
/Power/5.5V (Noisy) Supply/ENABLE: J803.2; also elsewhere on the board
/Power/5V0_USB: J801.1, J801.3, TP5.1; also elsewhere on the board
/Power/5V (Clean) Supply/ENABLE: J802.2; also elsewhere on the board
GND: J802.1, J803.1; also elsewhere on the board

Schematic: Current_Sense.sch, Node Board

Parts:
C1001, C1002, C1003, C1004: C; C_0805_HandSoldering
J1001, J1002, J1003, J1004: Conn_01x03; TE_3_pos_header_640456-3; Mfg. Part Num 640456-3
R1001, R1002, R1003, R1004, R1009, R1010, R1011, R1012, R1021, R1022, R1023, R1024: 0; R_0805_HandSoldering
R1005, R1006, R1007, R1008: 250; R_0805_HandSoldering
R1013, R1014, R1015, R1016: 40k; R_0805_HandSoldering
R1017, R1018, R1019, R1020: 10k; R_0805_HandSoldering
U1001, U1002: LM358; SOIC-8_3.9x4.9mm_Pitch1.27mm; Mfg. Part Num LM358ADR

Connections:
+5V: J1001.3, J1002.3, J1003.3, J1004.3, R1013.2, R1014.2, R1015.2, R1016.2, U1001.8 (V+), U1002.8 (V+); also elsewhere on the board
/Sensors/ADC/ADC_CH12: C1004.1, R1012.1, R1024.1; also elsewhere on the board
/Sensors/ADC/ADC_CH13: C1003.1, R1011.1, R1023.1; also elsewhere on the board
/Sensors/ADC/ADC_CH14: C1002.1, R1010.1, R1022.1; also elsewhere on the board
/Sensors/ADC/ADC_CH15: C1001.1, R1009.1, R1021.1; also elsewhere on the board
GND: C1001.2, C1002.2, C1003.2, C1004.2, J1001.1, J1002.1, J1003.1, J1004.1, R1005.2, R1006.2, R1007.2, R1008.2, U1001.4 (V-), U1002.4 (V-); also elsewhere on the board
unnamed: J1001.2, R1001.2, R1009.2
unnamed: J1002.2, R1002.2, R1010.2
unnamed: J1003.2, R1003.2, R1011.2
unnamed: J1004.2, R1004.2, R1012.2
unnamed: R1001.1, R1005.1, U1001.3 (+)
unnamed: R1002.1, R1006.1, U1001.5 (+)
unnamed: R1003.1, R1007.1, U1002.3 (+)
unnamed: R1004.1, R1008.1, U1002.5 (+)
unnamed: R1013.1, R1017.2, U1001.2 (-)
unnamed: R1014.1, R1018.2, U1001.6 (-)
unnamed: R1015.1, R1019.2, U1002.2 (-)
unnamed: R1016.1, R1020.2, U1002.6 (-)
unnamed: R1017.1, R1021.2, U1001.1
unnamed: R1018.1, R1022.2, U1001.7
unnamed: R1019.1, R1023.2, U1002.1
unnamed: R1020.1, R1024.2, U1002.7

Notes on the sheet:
Stuff bypass 0Ω and unstuff series 0Ωs converts to normal 0-5V input
Cap footing for optional LPF
Make sure to leave space around connector
Operating equation: V_out = 1.25 * (I_in*250Ω - 1V)

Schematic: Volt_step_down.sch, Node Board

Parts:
C1101, C1102: C; C_0805_HandSoldering
F1101, F1102: Fuse; R_1206_HandSoldering; Mfg. Part Num C1Q 250
J1101, J1102: Conn_01x03; TE_3_pos_header_640456-3; Mfg. Part Num 640456-3
R1101, R1102: 0; R_0805_HandSoldering
R1103, R1105: 82k; R_0805_HandSoldering
R1104, R1106: 20k; R_0805_HandSoldering

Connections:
+5V: R1101.1, R1102.1; also elsewhere on the board
+24V: F1101.1, F1102.1; also elsewhere on the board
/Sensors/ADC/ADC_CH6: C1101.1, R1103.2, R1104.1; also elsewhere on the board
/Sensors/ADC/ADC_CH7: C1102.1, R1105.2, R1106.1; also elsewhere on the board
GND: C1101.2, C1102.2, J1101.1, J1102.1, R1104.2, R1106.2; also elsewhere on the board
unnamed: F1101.2, J1101.3, R1101.2
unnamed: F1102.2, J1102.3, R1102.2
unnamed: J1101.2, R1103.1
unnamed: J1102.2, R1105.1

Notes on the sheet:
Silkscreen: DANGER, 24V power
Cap for optional LPF
For 0-5V operation, simply remove 20kΩ and replaced 82kΩ with a 0Ω

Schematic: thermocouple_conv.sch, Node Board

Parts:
C1201: 1uF; C_0805_HandSoldering
J1201, J1202, J1203, J1204, J1205, J1206: Conn_01x03; TE_3_pos_header_640456-3; Mfg. Part Num 640456-3
R1201: 45k; R_0805_HandSoldering
R1202: 5k; R_0805_HandSoldering
U1201: LMV601; SOT-363_SC-70-6_Handsoldering; Manufacturer P/N LMV601MG/NOPB

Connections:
+5V: C1201.2, J1201.3, J1202.3, J1203.3, J1204.3, J1205.3, J1206.3, R1201.1, U1201.5 (~EN), U1201.6 (V+); also elsewhere on the board
/Sensors/ADC/TC_to_Volt/tc_to_v_0/+IN: J1201.2; also elsewhere on the board
/Sensors/ADC/TC_to_Volt/tc_to_v_0/-IN: J1201.1; also elsewhere on the board
/Sensors/ADC/TC_to_Volt/tc_to_v_1/+IN: J1202.2; also elsewhere on the board
/Sensors/ADC/TC_to_Volt/tc_to_v_1/-IN: J1202.1; also elsewhere on the board
/Sensors/ADC/TC_to_Volt/tc_to_v_2/+IN: J1203.2; also elsewhere on the board
/Sensors/ADC/TC_to_Volt/tc_to_v_2/-IN: J1203.1; also elsewhere on the board
/Sensors/ADC/TC_to_Volt/tc_to_v_3/+IN: J1204.2; also elsewhere on the board
/Sensors/ADC/TC_to_Volt/tc_to_v_3/-IN: J1204.1; also elsewhere on the board
/Sensors/ADC/TC_to_Volt/tc_to_v_4/+IN: J1205.2; also elsewhere on the board
/Sensors/ADC/TC_to_Volt/tc_to_v_4/-IN: J1205.1; also elsewhere on the board
/Sensors/ADC/TC_to_Volt/tc_to_v_5/+IN: J1206.2; also elsewhere on the board
/Sensors/ADC/TC_to_Volt/tc_to_v_5/-IN: J1206.1; also elsewhere on the board
/Sensors/ADC/TC_to_Volt/tc_vref: U1201.3 (-), U1201.4; also elsewhere on the board
GND: C1201.1, R1202.2, U1201.2 (V-); also elsewhere on the board
unnamed: R1201.2, R1202.1, U1201.1 (+)

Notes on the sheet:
Reference Voltage for Cold Offset approx. 0.5V

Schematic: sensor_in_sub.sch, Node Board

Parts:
C1301, C1302, C1303, C1304: C; C_0805_HandSoldering
J1900, J1901, J1902, J1903: Conn_01x03; TE_3_pos_header_640456-3; Mfg. Part Num 640456-3
R1301, R1302, R1303, R1304: 0; R_0805_HandSoldering

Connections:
+5V: J1900.3, J1901.3, J1902.3, J1903.3; also elsewhere on the board
/Sensors/ADC/ADC_CH8: C1304.1, R1304.1; also elsewhere on the board
/Sensors/ADC/ADC_CH9: C1303.1, R1303.1; also elsewhere on the board
/Sensors/ADC/ADC_CH10: C1302.1, R1302.1; also elsewhere on the board
/Sensors/ADC/ADC_CH11: C1301.1, R1301.1; also elsewhere on the board
GND: C1301.2, C1302.2, C1303.2, C1304.2, J1900.1, J1901.1, J1902.1, J1903.1; also elsewhere on the board
unnamed: J1900.2, R1301.2
unnamed: J1901.2, R1302.2
unnamed: J1902.2, R1303.2
unnamed: J1903.2, R1304.2

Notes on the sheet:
Optional LPF

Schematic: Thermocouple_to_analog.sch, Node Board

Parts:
C1305, C1307, C1308: 0.1uF; C_0805_HandSoldering; Digikey P/N 311-1088-1-ND
C1306: 1uF; C_0805_HandSoldering; Digikey P/N 1276-1946-1-ND
R1305: 1M; R_0805_HandSoldering; Digikey P/N 311-1.00MHRCT-ND
R1306, R1307: 150; R_0805_HandSoldering; Digikey P/N 311-150HRCT-ND
R1308: 0; R_0805_HandSoldering
U1301: AD849X; MSOP-8_3x3mm_Pitch0.65mm; Manufacturer P/N AD8495ARMZ-R7

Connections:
+5V: C1308.2, U1301.7 (+Vs); also elsewhere on the board
/Sensors/ADC/ADC_CH0: R1308.1, U1301.5 (SENSE), U1301.6 (OUT); also elsewhere on the board
/Sensors/ADC/TC_to_Volt/tc_to_v_0/+IN: R1307.2, R1308.2; also elsewhere on the board
/Sensors/ADC/TC_to_Volt/tc_to_v_0/-IN: R1305.2, R1306.2; also elsewhere on the board
/Sensors/ADC/TC_to_Volt/tc_vref: U1301.2 (REF); also elsewhere on the board
GND: C1305.1, C1307.2, C1308.1, R1305.1, U1301.3 (-Vs); also elsewhere on the board
unnamed: C1305.2, C1306.2, R1306.1, U1301.1 (-In)
unnamed: C1306.1, C1307.1, R1307.1, U1301.8 (+IN)

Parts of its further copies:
C1401, C1403, C1404, C1518, C1520, C1521, C1601, C1603, C1604, C1708, C1710, C1711, C1801, C1803, C1804: 0.1uF; C_0805_HandSoldering; Digikey P/N 311-1088-1-ND
C1402, C1519, C1602, C1709, C1802: 1uF; C_0805_HandSoldering; Digikey P/N 1276-1946-1-ND
R1401, R1510, R1601, R1703, R1801: 1M; R_0805_HandSoldering; Digikey P/N 311-1.00MHRCT-ND
R1402, R1403, R1511, R1512, R1602, R1603, R1704, R1705, R1802, R1803: 150; R_0805_HandSoldering; Digikey P/N 311-150HRCT-ND
R1404, R1513, R1604, R1706, R1804: 0; R_0805_HandSoldering
U1401, U1508, U1601, U1702, U1801: AD849X; MSOP-8_3x3mm_Pitch0.65mm; Manufacturer P/N AD8495ARMZ-R7

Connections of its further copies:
+5V: C1404.2, C1521.2, C1604.2, C1711.2, C1804.2, U1401.7 (+Vs), U1508.7 (+Vs), U1601.7 (+Vs), U1702.7 (+Vs), U1801.7 (+Vs); also elsewhere on the board
/Sensors/ADC/ADC_CH1: R1404.1, U1401.5 (SENSE), U1401.6 (OUT); also elsewhere on the board
/Sensors/ADC/ADC_CH2: R1513.1, U1508.5 (SENSE), U1508.6 (OUT); also elsewhere on the board
/Sensors/ADC/ADC_CH3: R1604.1, U1601.5 (SENSE), U1601.6 (OUT); also elsewhere on the board
/Sensors/ADC/ADC_CH4: R1706.1, U1702.5 (SENSE), U1702.6 (OUT); also elsewhere on the board
/Sensors/ADC/ADC_CH5: R1804.1, U1801.5 (SENSE), U1801.6 (OUT); also elsewhere on the board
/Sensors/ADC/TC_to_Volt/tc_to_v_1/+IN: R1403.2, R1404.2; also elsewhere on the board
/Sensors/ADC/TC_to_Volt/tc_to_v_1/-IN: R1401.2, R1402.2; also elsewhere on the board
/Sensors/ADC/TC_to_Volt/tc_to_v_2/+IN: R1512.2, R1513.2; also elsewhere on the board
/Sensors/ADC/TC_to_Volt/tc_to_v_2/-IN: R1510.2, R1511.2; also elsewhere on the board
/Sensors/ADC/TC_to_Volt/tc_to_v_3/+IN: R1603.2, R1604.2; also elsewhere on the board
/Sensors/ADC/TC_to_Volt/tc_to_v_3/-IN: R1601.2, R1602.2; also elsewhere on the board
/Sensors/ADC/TC_to_Volt/tc_to_v_4/+IN: R1705.2, R1706.2; also elsewhere on the board
/Sensors/ADC/TC_to_Volt/tc_to_v_4/-IN: R1703.2, R1704.2; also elsewhere on the board
/Sensors/ADC/TC_to_Volt/tc_to_v_5/+IN: R1803.2, R1804.2; also elsewhere on the board
/Sensors/ADC/TC_to_Volt/tc_to_v_5/-IN: R1801.2, R1802.2; also elsewhere on the board
/Sensors/ADC/TC_to_Volt/tc_vref: U1401.2 (REF), U1508.2 (REF), U1601.2 (REF), U1702.2 (REF), U1801.2 (REF); also elsewhere on the board
GND: C1401.1, C1403.2, C1404.1, C1518.1, C1520.2, C1521.1, C1601.1, C1603.2, C1604.1, C1708.1, C1710.2, C1711.1, C1801.1, C1803.2, C1804.1, R1401.1, R1510.1, R1601.1, R1703.1, R1801.1, U1401.3 (-Vs), U1508.3 (-Vs), U1601.3 (-Vs), U1702.3 (-Vs), U1801.3 (-Vs); also elsewhere on the board
unnamed: C1401.2, C1402.2, R1402.1, U1401.1 (-In)
unnamed: C1402.1, C1403.1, R1403.1, U1401.8 (+IN)
unnamed: C1518.2, C1519.2, R1511.1, U1508.1 (-In)
unnamed: C1519.1, C1520.1, R1512.1, U1508.8 (+IN)
unnamed: C1601.2, C1602.2, R1602.1, U1601.1 (-In)
unnamed: C1602.1, C1603.1, R1603.1, U1601.8 (+IN)
unnamed: C1708.2, C1709.2, R1704.1, U1702.1 (-In)
unnamed: C1709.1, C1710.1, R1705.1, U1702.8 (+IN)
unnamed: C1801.2, C1802.2, R1802.1, U1801.1 (-In)
unnamed: C1802.1, C1803.1, R1803.1, U1801.8 (+IN)

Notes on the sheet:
Low Pass Filter
Filter Freq, Diff: 505.2 Hz Filter Freq, CM: 10610.3 Hz

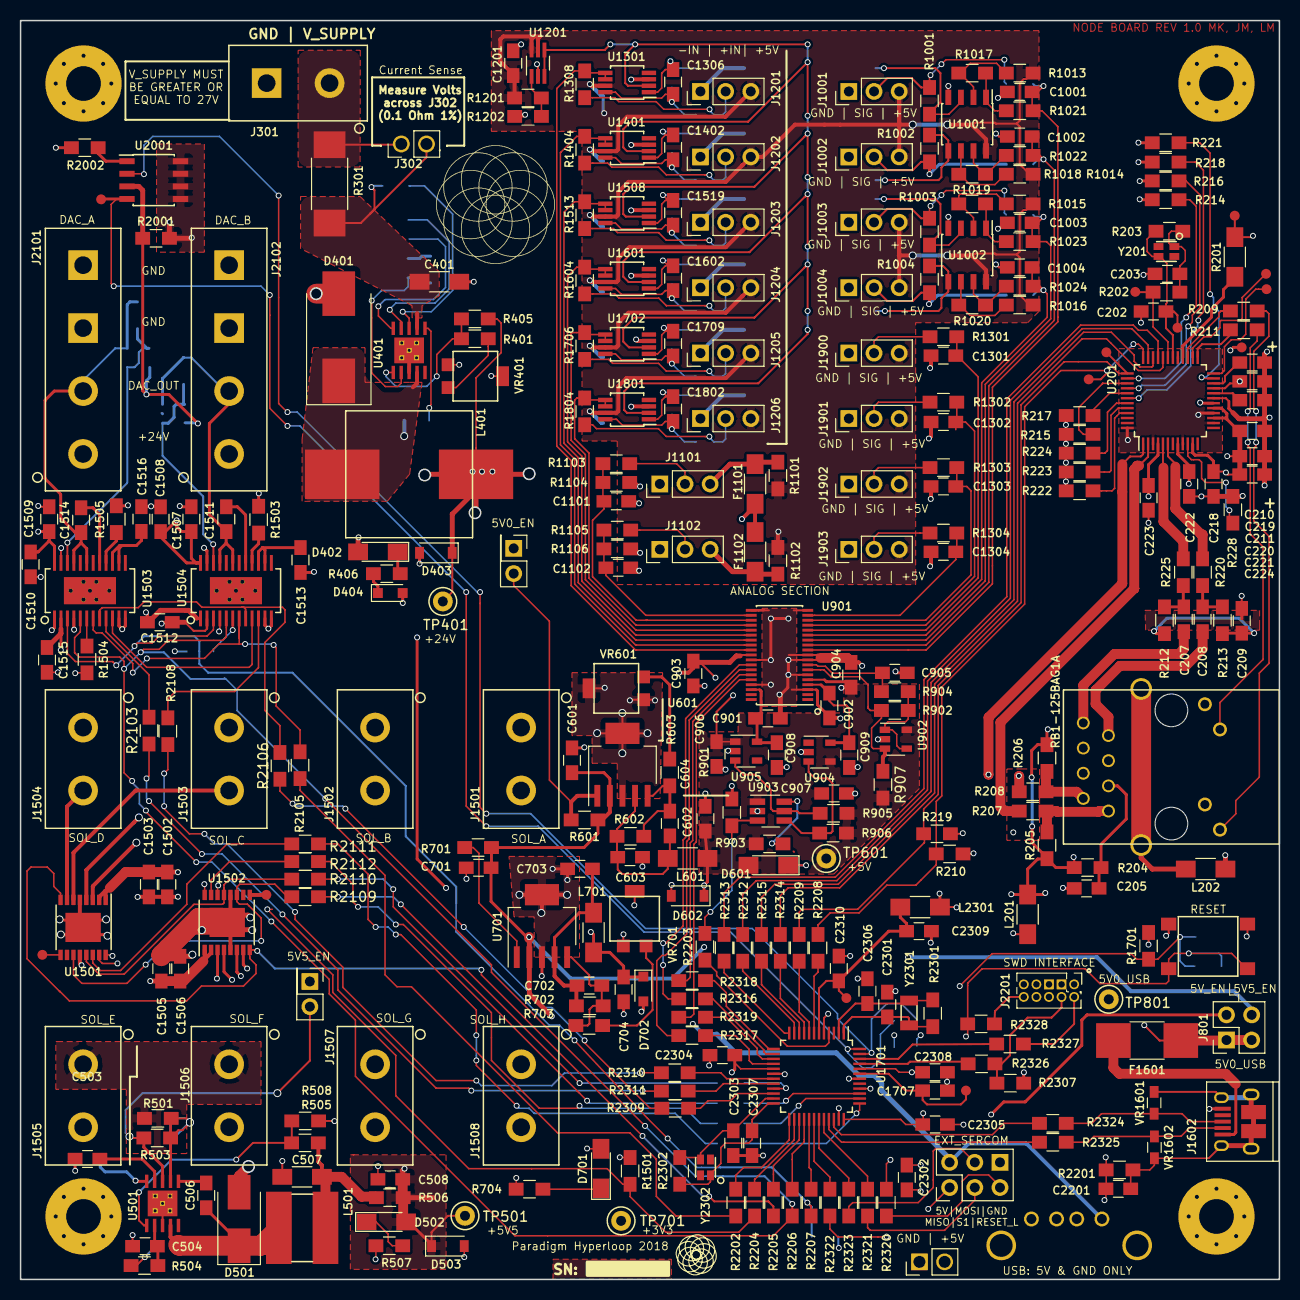
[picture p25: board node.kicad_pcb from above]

Board: 4 copper layers, 127.0 x 127.0 mm, 399 parts (0 on the bottom side), 258 nets.

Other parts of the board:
J2101, J2102: CONN_01X04; Molex_4pin_power_10-84-4042
P2101: USB_B; USB_A
TP401, TP501, TP601, TP701, TP801: Test_Point; Test_Point_Keystone_5000-5004_Miniature

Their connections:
+3V3: TP701.1; also elsewhere on the board
+5V: P2101.1, TP601.1; also elsewhere on the board
+24V: J2101.1, J2102.1, TP401.1; also elsewhere on the board
/Actuator Interface/DAC1_VIOUT: J2101.2; also elsewhere on the board
/Actuator Interface/DAC2_VIOUT: J2102.2; also elsewhere on the board
/Power/3.3V (Clean) Supply/5V5: TP501.1; also elsewhere on the board
/Power/5V0_USB: TP801.1; also elsewhere on the board
GND: J2101.3, J2101.4, J2102.3, J2102.4, P2101.4, P2101.5; also elsewhere on the board

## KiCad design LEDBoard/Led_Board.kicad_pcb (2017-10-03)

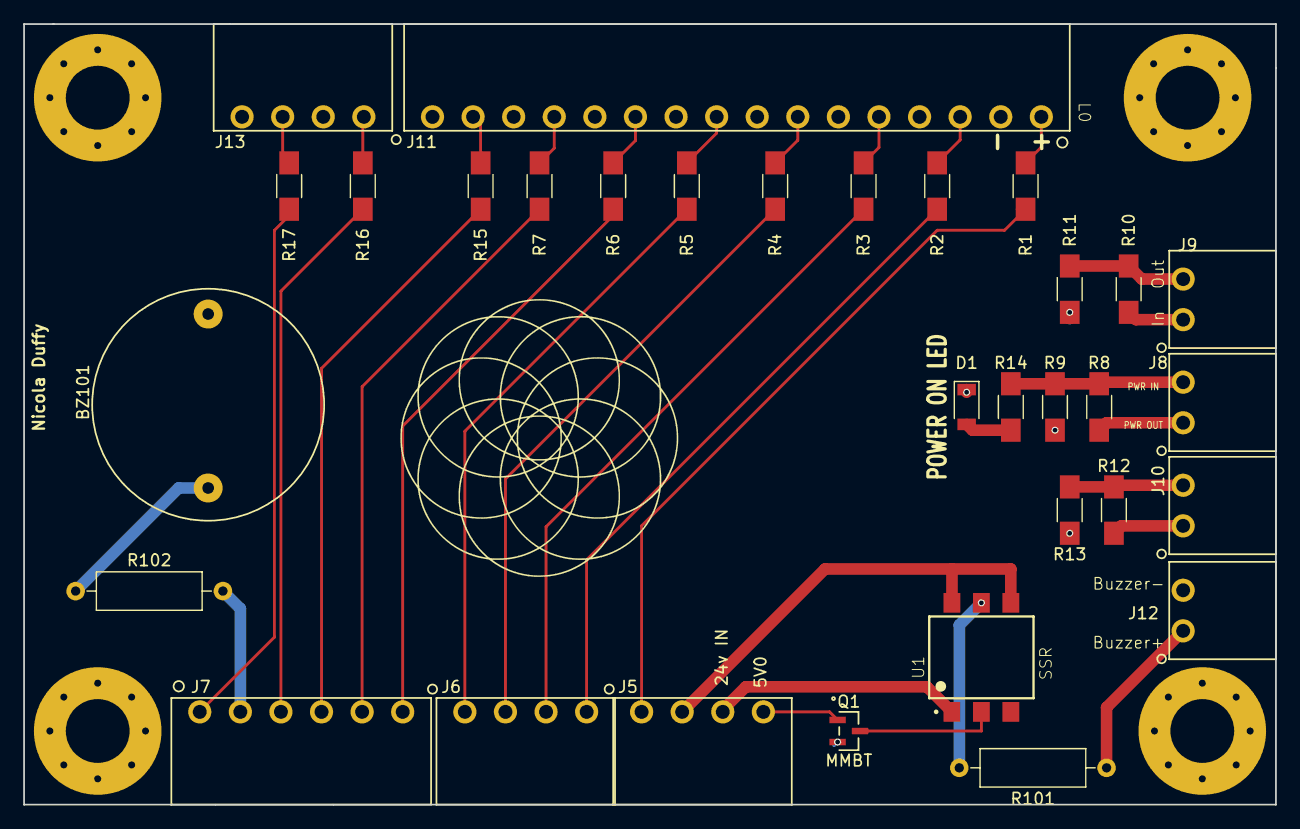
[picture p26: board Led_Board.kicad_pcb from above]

Board: 2 copper layers, 107.9 x 67.3 mm, 36 parts (0 on the bottom side), 36 nets.

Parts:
BZ101: nicolaBuzzer
D1: D_1206
J1, J2, J3, J4: MountingHole_5.5mm_Pad_Via
J5, J6, J13: CONN_PHOENIX_1844236_4PIN
J7: CONN_PHOENIX_1844252_6PIN
J8, J9, J10, J12: CONN_PHOENIX_1844210_2PIN
J11: CONN_PHOENIX_1844359_16PIN
Q1: MMBT; MMBF170LT1G
R1, R2, R3, R4, R5, R6, R7, R8, R9, R10, R11, R12, R13, R14, R15, R16, R17: R_1206_HandSoldering
R101, R102: R_Axial_DIN0309_L9.0mm_D3.2mm_P12.70mm_Horizontal
U1: SSR; SOIC254P1005X390-6N

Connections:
/5V: J7.2, R102.2
/5V0: J5.3, U1.1
/24V: J5.2, U1.4, U1.6
/A0: J5.1, R1.2
/A1: J6.4, R2.2
/A2: J6.3, R3.2
/A3: J6.2, R4.2
/A4: J6.1, R5.2
/A5: J7.6, R6.2
/A6: J7.5, R7.2
/A7: J7.4, R15.2
/A8: J7.3, R16.2
/ArduinoLED: J7.1, R17.2
/Buzzer: J12.1, R101.1
/GND: BZ101.2, D1.1, J1.1, J2.1, J3.1, J4.1, J11.2, J11.4, J11.6, J11.8, J11.10, J11.12, J11.14, J11.16, J12.2, J13.2, J13.4, Q1.2, R9.2, R11.2, R13.2
/L0: J11.1, R1.1
/L1: J11.3, R2.1
/L2: J11.5, R3.1
/L3: J11.7, R4.1
/L4: J11.9, R5.1
/L5: J11.11, R6.1
/L6: J11.13, R7.1
/L7: J11.15, R15.1
/L8: J13.1, R16.1
/L9: J13.3, R17.1
/Transistor: J5.4, Q1.1
/VDI0: J8.1, R8.1
/VDI1: J9.1, R10.1
/VDI2: J10.1, R12.1
/VDO0: J8.2, R8.2, R9.1, R14.1
/VDO1: J9.2, R10.2, R11.1
/VDO2: J10.2, R12.2, R13.1
unnamed: BZ101.1, R102.1
unnamed: D1.2, R14.2
unnamed: Q1.3, U1.2
unnamed: R101.2, U1.5

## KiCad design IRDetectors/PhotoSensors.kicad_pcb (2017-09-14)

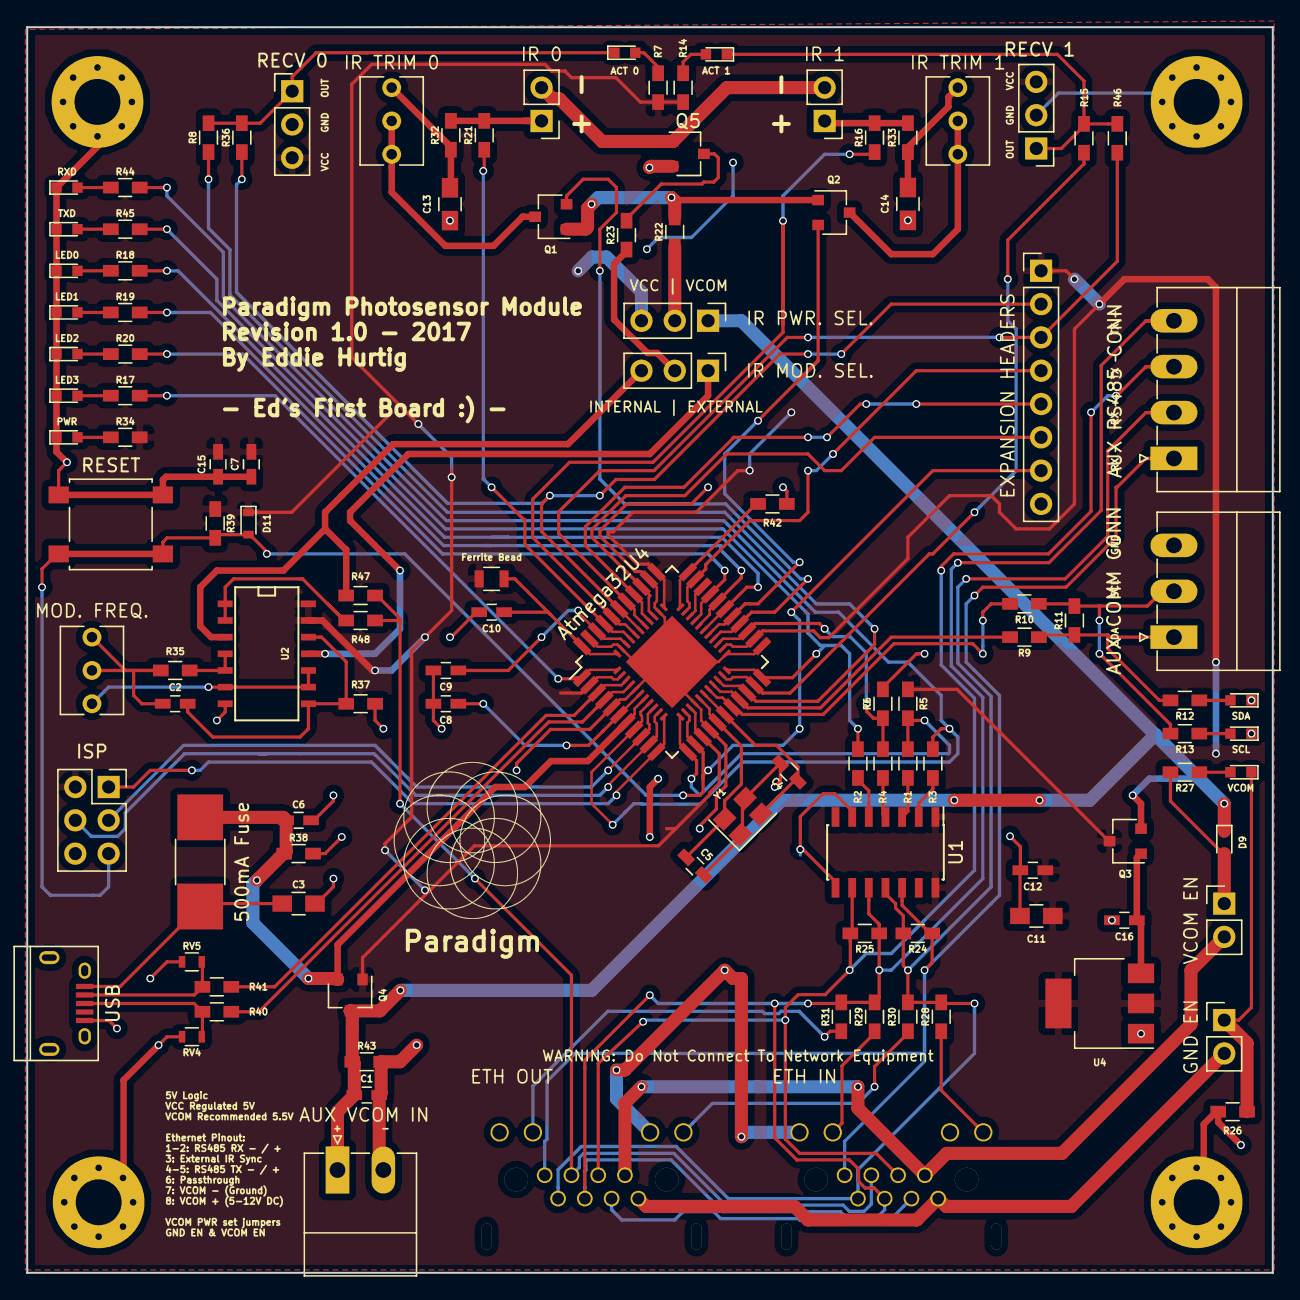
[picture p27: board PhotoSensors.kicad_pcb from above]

Board: 2 copper layers, 95.0 x 95.0 mm, 112 parts (0 on the bottom side), 92 nets.

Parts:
500mA Fuse: 500mA; R_1812_HandSoldering
ACT 0: D0_ACT; LED_0603
ACT 1: D1_ACT; LED_0603
AUX COMM CONN: I2C _CONN; PhoenixContact_MC-G_03x3.50mm_Angled
AUX RS485 CONN: RS485_CONN; PhoenixContact_MC-G_04x3.50mm_Angled
AUX VCOM IN: PWR_IN; PhoenixContact_MC-G_02x3.50mm_Angled
Atmega32U4: ATMEGA32U4RC-A; QFN-44_7x7mm_Combined_TQFP-44_10x10mm_Pitch0.8mm
C1, C2: 10n; C_0603_HandSoldering
C3, C11: 22u; C_0805_HandSoldering
C4, C5: 22p; C_0603_HandSoldering
C6, C7, C9, C12, C15, C16: 100n; C_0603_HandSoldering
C8, C10: 1u; C_0603_HandSoldering
C13, C14: 10u; C_0805_HandSoldering
D9: D_VCOM; D_0603
D11: D_RST; D_0603
EXPANSION HEADERS: CONN_01X08; Pin_Header_Straight_1x08_Pitch2.54mm
Ferrite Bead: Ferrite_Bead; R_0805
GND EN: GND_EN; Pin_Header_Straight_1x02_Pitch2.54mm
IR 0: CONN_IR0; Pin_Header_Straight_1x02_Pitch2.54mm
IR 1: CONN_IR1; Pin_Header_Straight_1x02_Pitch2.54mm
IR MOD. SEL.: IR_SYNC_SELECT; Pin_Header_Straight_1x03_Pitch2.54mm
IR PWR. SEL.: Emitter Current Source; Pin_Header_Straight_1x03_Pitch2.54mm
IR TRIM 0, IR TRIM 1: RP500; Potentiometer_Trimmer_Vishay_T73XW_Vertical
ISP: ISP; Socket_Strip_Straight_2x03_Pitch2.54mm
J1, J2: RJ45_LEDS; RJ45_8P8C_90DEG_LEDs
LED0: LED1; LED_0603
LED1: LED2; LED_0603
LED2: LED3; LED_0603
LED3: LED0; LED_0603
MOD. FREQ.: POT_TRIM; Potentiometer_Trimmer_Vishay_T73XW_Vertical
PWR: PWR_LED; LED_0603
Q1, Q2, Q4: FDN340PCT-ND; SC-59
Q3: FDN340PCT; SC-59
Q5: Q_PMOS_SDG; SC-59
R1, R2, R3, R4, R16, R21, R23, R26, R32, R33, R36, R46, R48: 0; R_0603_HandSoldering
R5, R6: 20k; R_0603_HandSoldering
R7, R12, R13, R14, R17, R18, R19, R20, R27, R28, R29, R30, R31, R34, R44, R45: 1k; R_0603_HandSoldering
R8, R15: 220; R_0603_HandSoldering
R9, R10, R11, R47: DNS; R_0603_HandSoldering
R22: 470; R_0603_HandSoldering
R24, R25: 120; R_0603_HandSoldering
R35: 100k; R_0603_HandSoldering
R37, R38, R39, R42, R43: 10k; R_0603_HandSoldering
R40, R41: 22R; R_0603_HandSoldering
RECV 0: CONN_PD0; Pin_Header_Straight_1x03_Pitch2.54mm
RECV 1: CONN_PD1; Pin_Header_Straight_1x03_Pitch2.54mm
RESET: RESET_BTN; SW_SPST_B3S-1000
RV4, RV5: CG0603MLC; R_0603
RXD: RX_LED; LED_0603
SCL: SCL; LED_0603
SDA: SDA; LED_0603
TXD: TX_LED; LED_0603
U1: MAX13432EETD; SOIC-14_3.9x8.7mm_Pitch1.27mm
U2: 7400; SOIC-14_N
U4: NCP1117ST50T3GOSCT; SOT-223
USB: USB_MICRO; USB_Micro-B
VCOM: VCOM_PWR; LED_0603
VCOM EN: VCOM_EN; Pin_Header_Straight_1x02_Pitch2.54mm
Y1: Crystal; Crystal_SMD_Abracon_ABM8G-4pin_3.2x2.5mm

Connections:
/ADC4: Atmega32U4.39, EXPANSION HEADERS.2, R36.1
/ADC5: Atmega32U4.38, EXPANSION HEADERS.3, R46.1
/Atmega/D+: Atmega32U4.4, R40.1
/Atmega/D-: Atmega32U4.3, R41.1
/Atmega/MISO: Atmega32U4.11, ISP.1
/Atmega/MOSI: Atmega32U4.10, ISP.4
/Atmega/PC7: Atmega32U4.32, EXPANSION HEADERS.4
/Atmega/PF6: Atmega32U4.37, EXPANSION HEADERS.5
/Atmega/PF7: Atmega32U4.36, EXPANSION HEADERS.6
/Atmega/SCK: Atmega32U4.9, ISP.3
/Atmega/XTAL1: Atmega32U4.17, C4.1, Y1.2
/Atmega/XTAL2: Atmega32U4.16, C5.1, Y1.4
/D0_OUT: ACT 0.1, R8.2, R36.2, RECV 0.1
/D1_OUT: ACT 1.1, R15.2, R46.2, RECV 1.1
/DE: Atmega32U4.12, R1.1, R5.1
/EXT_SYNC: J1.3, J2.3, R47.1, R48.1
/INT0: Atmega32U4.20, R8.1
/INT1: Atmega32U4.21, R15.1
/IR0_+: IR 0.1, R21.2, R32.2
/IR0_-: IR 0.2, IR 1.2, Q5.1
/IR0_ADC: Atmega32U4.41, R21.1
/IR0_SETPOINT: Atmega32U4.26, Q1.2
/IR1_+: IR 1.1, R16.1, R33.2
/IR1_ADC: Atmega32U4.40, R16.2
/IR1_SETPOINT: Atmega32U4.27, Q2.2
/LED0: Atmega32U4.1, R17.2
/LED1: Atmega32U4.28, R18.2
/LED2: Atmega32U4.29, R19.2
/LED3: Atmega32U4.30, R20.2
/RE: Atmega32U4.25, R4.1, R6.2
/RESET: Atmega32U4.13, D11.2, EXPANSION HEADERS.7, ISP.5, R39.2, RESET.2
/RS422_Transiever/DE: R1.2, U1.3
/RS422_Transiever/RE: R4.2, U1.4
/RS422_Transiever/RS485_RX_+: AUX RS485 CONN.2, J1.2, J2.2, R24.1, R28.2, R30.2, U1.11
/RS422_Transiever/RS485_RX_-: AUX RS485 CONN.1, J1.1, J2.1, R24.2, U1.12
/RS422_Transiever/RS485_TX_+: AUX RS485 CONN.4, J1.4, J2.4, R25.1, R29.2, R31.2, U1.10
/RS422_Transiever/RS485_TX_-: AUX RS485 CONN.3, J1.5, J2.5, R25.2, U1.9
/RS422_Transiever/RXD: R3.2, U1.2
/RS422_Transiever/TXD: R2.2, U1.5
/RXD: Atmega32U4.8, R3.1, R44.2
/SCL: Atmega32U4.18, R10.2
/SDA: Atmega32U4.19, R9.2
/TXD: Atmega32U4.22, R2.1, R45.2
GND: AUX COMM CONN.3, AUX VCOM IN.2, Atmega32U4.5, Atmega32U4.15, Atmega32U4.23, Atmega32U4.35, Atmega32U4.43, C1.2, C3.2, C4.2, C5.2, C6.2, C7.1, C8.2, C9.2, C10.2, C11.2, C12.2, C13.1, C14.1, C15.1, C16.2, EXPANSION HEADERS.8, ISP.6, J1.9, J1.11, J2.9, J2.11, LED0.1, LED1.1, LED2.1, LED3.1, PWR.1, Q5.2, R6.1, R26.2, R37.2, R38.2, R42.1, R43.1, RECV 0.2, RECV 1.2, RESET.1, RV4.1, RV5.1, RXD.1, SCL.1, SDA.1, TXD.1, U1.6, U1.8, U2.7, U4.1, USB.5, USB.6, Y1.1, Y1.3
unnamed: C2.1, MOD. FREQ..1, MOD. FREQ..2, R35.1
unnamed: C2.2, R37.1, U2.8, U2.12
unnamed: 500mA Fuse.2, C3.1, USB.1
unnamed: Atmega32U4.6, C8.1
unnamed: Atmega32U4.42, C9.1
unnamed: Atmega32U4.44, C10.1, Ferrite Bead.1
unnamed: C13.2, IR TRIM 0.3, R32.1
unnamed: C14.2, IR TRIM 1.3, R33.1
unnamed: C16.1, Q3.1, U4.3
unnamed: ACT 0.2, R7.2
unnamed: R12.2, SDA.2
unnamed: R13.2, SCL.2
unnamed: ACT 1.2, R14.2
unnamed: LED3.2, R17.1
unnamed: LED0.2, R18.1
unnamed: LED1.2, R19.1
unnamed: LED2.2, R20.1
unnamed: D9.2, R27.2, VCOM EN.1
unnamed: GND EN.1, R26.1, VCOM.1
unnamed: R27.1, VCOM.2
unnamed: PWR.2, R34.1
unnamed: R44.1, RXD.2
unnamed: R45.1, TXD.2
unnamed: MOD. FREQ..3, U2.6, U2.9, U2.10
unnamed: J1.7, J2.7, VCOM EN.2
unnamed: GND EN.2, J1.8, J2.8
unnamed: J1.10, R29.1
unnamed: J1.12, R28.1
unnamed: J2.10, R31.1
unnamed: J2.12, R30.1
unnamed: IR PWR. SEL..2, R22.1
unnamed: IR MOD. SEL..1, U2.11
unnamed: IR MOD. SEL..2, R23.1
unnamed: IR MOD. SEL..3, R47.2, U2.3
unnamed: AUX COMM CONN.1, R9.1, R11.1, R12.1
unnamed: AUX COMM CONN.2, R10.1, R11.2, R13.1
unnamed: R41.2, RV5.2, USB.2
unnamed: R40.2, RV4.2, USB.3
unnamed: Q1.1, Q2.1, R22.2
unnamed: IR TRIM 0.1, IR TRIM 0.2, Q1.3
unnamed: IR TRIM 1.1, IR TRIM 1.2, Q2.3
unnamed: Q5.3, R23.2
unnamed: R35.2, U2.4, U2.5
unnamed: Atmega32U4.33, R42.2
unnamed: R48.2, U2.1, U2.2
VCC: Atmega32U4.2, Atmega32U4.14, Atmega32U4.24, Atmega32U4.34, C7.2, C11.1, C12.1, C15.2, D11.1, EXPANSION HEADERS.1, Ferrite Bead.2, IR PWR. SEL..3, ISP.2, Q3.3, Q4.1, R5.2, R7.1, R14.1, R34.2, R39.1, RECV 0.3, RECV 1.3, U1.1, U1.14, U2.13, U2.14, U4.2, U4.4
VCOM: AUX VCOM IN.1, C1.1, D9.1, IR PWR. SEL..1, Q3.2, Q4.3, R43.2
VUSB: 500mA Fuse.1, Atmega32U4.7, C6.1, Q4.2, R38.1

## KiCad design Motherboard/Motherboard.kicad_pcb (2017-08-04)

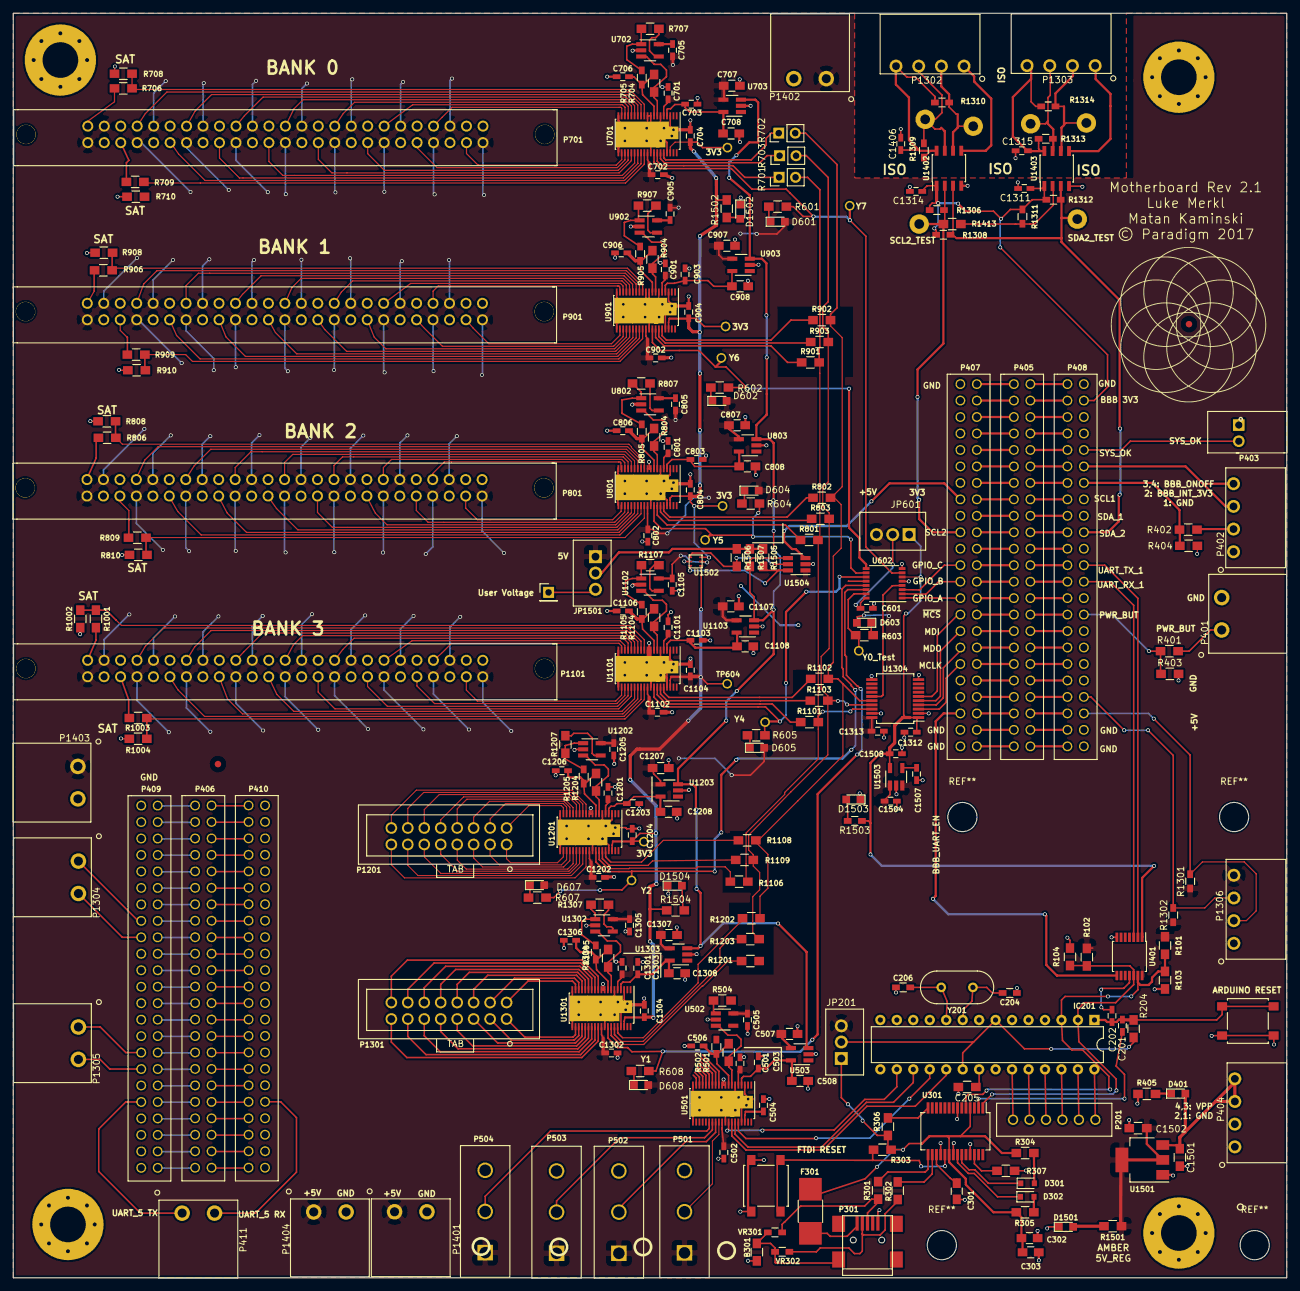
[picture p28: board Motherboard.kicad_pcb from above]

Board: 2 copper layers, 196.4 x 195.1 mm, 283 parts (0 on the bottom side), 350 nets.

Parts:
B301: Ferrite__BLM21_Murata; R_0805_HandSoldering
C201, C202, C1311, C1312, C1313, C1314, C1315, C1406: 0.1uF; C_0603_HandSoldering
C204, C206: 22pF; R_0603_HandSoldering
C205: SAT; R_0805_HandSoldering
C301, C302: 100nF; C_0805_HandSoldering
C303: 4.7uF; C_0805_HandSoldering
C501, C502, C504, C505, C601, C701, C702, C704, C705, C801, C802, C804, C805, C901, C902, C904, C905, C1101, C1102, C1104, C1201, C1202, C1204, C1205, C1301, C1302, C1304, C1305, C1504: 1uF; C_0603_HandSoldering
C503, C703, C803, C903, C1103, C1105, C1203, C1303: 10uF; C_0603_HandSoldering
C506, C706, C806, C906, C1106, C1206, C1306: 150pF; C_0603_HandSoldering
C507, C508, C707, C708, C807, C808, C907, C908, C1107, C1108, C1207, C1208, C1307, C1308: 0.1uF; C_0805_HandSoldering
C1501, C1502: 10uf; R_0805_HandSoldering
C1507: 10nF; C_0603_HandSoldering
C1508: 2.2uF; C_0603_HandSoldering
D301: TX_LED; D_0805
D302: RX_LED; D_0805
D401: BLUE_LED; LED_0805
D601, D602, D603, D604, D605, D607, D608, D1502, D1503, D1504: GREEN_LED; LED_0805
D1501: AMBER_LED; LED_0805
F301: FUSE; R_1812_HandSoldering
IC201: ATMEGA328-P; DIP-28_W7.62mm
J132, J132#2, J132#3, J132#4: MOUNTING_HOLE; MountingHole_5.5mm_Pad_Via
JP201, JP601, JP1501: JUMPER3; Wafer_Vertical10x5.8x7RM2.5-3
P201: CONN_01X06; quick_6pin_2.54mm
P301: USB_OTG; USB_Mini-B
P401, P411, P1304, P1305, P1401, P1402, P1403, P1404: CONN_01X02; CONN_PHOENIX_1923869_2PIN
P402, P404, P1302, P1303: CONN_01X04; CONN_PHOENIX_1844236_4PIN
P403: CONN_01X02; pheonix_2pin_screwTerminal
P405: BeagleboneBlack_P9; header_2.54x2.54mm_spacing_pinName
P406: BeagleboneBlack_P8; header_2.54x2.54mm_spacing_pinName
P407, P408, P409, P410: CONN_02X23; header_2.54x2.54mm_spacing_pinName
P501, P502, P503, P504: CONN_01X03; 3POS_Header_TEConn_6.35mm_pitch
P701, P801, P901, P1101: CONN_02X25; 3M_50pos_latching_numbers_matchModule
P1201, P1301: CONN_02X08; OnShore_16Pin_Vert_2.54mm_spacing
P1306: CONN_01X04; CONN_PHOENIX_1844236_4PIN_1
P1406: CONN_01X01; Pin_Header_Straight_1x01_Pitch2.54mm
R101, R102, R103, R104, R706, R708, R709, R710, R806, R808, R809, R810, R906, R908, R909, R910, R1001, R1002, R1003, R1004: SAT; R_0805_HandSoldering
R204, R303, R306: 10K; R_0805_HandSoldering
R301, R302: 22; R_0805_HandSoldering
R304, R305: 270; R_0805_HandSoldering
R307, R501, R504, R704, R707, R801, R802, R803, R804, R807, R901, R902, R903, R904, R907, R1101, R1102, R1103, R1104, R1106, R1107, R1109, R1201, R1202, R1203, R1204, R1207, R1304, R1307, R1413: 0; R_0805_HandSoldering
R401, R402, R405: 10k; R_0805_HandSoldering
R403, R404: 15k; R_0805_HandSoldering
R502, R705, R805, R905, R1105, R1205, R1305: 100; R_0603_HandSoldering
R601, R602, R603, R604, R605, R607, R608: 590; R_0805_HandSoldering
R701, R702, R703: 0; Pin_Header_Straight_1x02_Pitch2.54mm
R1108: 100; R_0805_HandSoldering
R1301, R1302, R1306, R1308, R1309, R1310, R1311, R1312, R1313, R1314: 1.5k; R_0603_HandSoldering
R1501, R1502, R1504: 300; R_0805_HandSoldering
R1503: 300; R_0603_HandSoldering
R1505, R1506, R1507: 100k; R_0805_HandSoldering
SW201, SW301: SW_PUSH; SW_SPST_B3S-1000
TP601, TP602, TP603, TP604, TP607, TP611, TP612, TP613, TP614, TP616, TP618, TP1401, TP1402, TP1403, TP1404, TP1405, TP1406: TP; Measurement_Point_Round-TH_Big
U301: FT232RL; SSOP-28_5.3x10.2mm_Pitch0.65mm
U401: LEVEL_SHIFT_NXP_14TSSOP; TSSOP-14_4.4x5mm_Pitch0.65mm
U501, U701, U801, U901, U1101, U1201, U1301: ADS7953_38TSSOP; TSSOP-38_4.4x9.7mm_Pitch0.5mm
U502, U702, U802, U902, U1102, U1202, U1302: OPA192; SOT-23-5_HandSoldering
U503, U703, U803, U903, U1103, U1203, U1303: LM4132_TexasInstruments__LDO_REF; SOT-23-5_HandSoldering
U602: DEMUX_1to8_TI; TSSOP-16-1EP_4.4x5mm_Pitch0.65mm
U1304: ADuM3150_AnalogDev_7CH_ISO; SSOP-20_5.3x7.2mm_Pitch0.65mm
U1402, U1403: I2C_ISO_TI_ISO1541; SOIC-8_3.9x4.9mm_Pitch1.27mm
U1501: NCP1117ST50T3G_MountingTab; SOT-223
U1502: TPS719XX_TexasInstruments_2x2SON; TPS719XX_TexasInstruments_2x2_mm_SON
U1503: LP2985-N; SOT-23-5_HandSoldering
U1504: LM3880_TexasInstruments_PWR_SEQ; SOT-23-6_Handsoldering
VR301, VR302: 5V; R_0603_HandSoldering
Y201: 16MHz; Crystal_HC49-U_Vertical

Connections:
+3V3: C704.1, C804.1, C904.1, C1204.1, C1304.1, C1312.2, C1508.2, JP601.1, R1502.1, R1503.1, R1504.1, TP601.1, TP602.1, TP603.1, TP604.1, TP607.1, U401.1, U501.36, U602.6, U701.36, U801.36, U901.36, U1101.36, U1201.36, U1301.36, U1304.1, U1502.1, U1502.3, U1503.5
+5F: C302.1, C303.1, F301.2, JP201.1, R303.2, R304.1, R305.1, R306.2, U301.4, U301.20
+5V: C501.2, C502.1, C505.2, C507.1, C701.2, C702.1, C705.1, C707.1, C801.2, C802.1, C805.1, C807.1, C901.2, C902.1, C905.1, C907.1, C1101.2, C1102.1, C1104.1, C1107.1, C1201.2, C1202.1, C1205.2, C1207.1, C1301.2, C1302.1, C1305.2, C1307.1, C1313.1, C1502.1, C1504.2, D601.2, D602.2, D603.2, D604.2, D605.2, D607.2, D608.2, JP201.3, JP601.3, JP1501.1, P501.1, P502.1, P503.1, P504.1, P701.1, P701.4, P701.7, P701.10, P701.13, P701.16, P701.19, P701.22, P701.25, P701.28, P701.31, P701.34, P701.37, P701.40, P701.43, P701.46, P701.49, P801.1, P801.4, P801.7, P801.10, P801.13, P801.16, P801.19, P801.22, P801.25, P801.28, P801.31, P801.34, P801.37, P801.40, P801.43, P801.46, P801.49, P901.1, P901.4, P901.7, P901.10, P901.13, P901.16, P901.19, P901.22, P901.25, P901.28, P901.31, P901.34, P901.37, P901.40, P901.43, P901.46, P901.49, P1101.1, P1101.4, P1101.7, P1101.10, P1101.13, P1101.16, P1101.19, P1101.22, P1101.25, P1101.28, P1101.31, P1101.34, P1101.37, P1101.40, P1101.43, P1101.46, P1101.49, P1306.4, P1401.1, P1402.1, P1403.1, P1404.1, R101.1, R102.1, R1301.1, R1302.1, R1501.1, U401.14, U501.5, U501.29, U502.5, U503.4, U701.5, U701.29, U702.5, U703.4, U801.5, U801.29, U802.5, U803.4, U901.5, U901.29, U902.5, U903.4, U1101.5, U1101.29, U1102.5, U1103.4, U1201.5, U1201.29, U1202.5, U1203.4, U1301.5, U1301.29, U1302.5, U1303.4, U1304.20, U1501.2, U1501.4, U1502.2, U1503.1, U1503.3, U1504.1
/BBB_3V3: C1311.2, C1314.2, P408.4, R1306.1, R1308.1, R1311.1, R1312.1, U1402.1, U1403.1
/CTS: IC201.4, IC201.5
/DTR_BBB: C202.1, U401.4, U401.11
/DTR_FTDI: C201.1, U301.2
/GPIO_A: P407.27, U602.1
/GPIO_B: P407.25, U602.2
/GPIO_C: P407.23, U602.3
/MCLK: P407.35, U1304.3
/MDI: P407.31, U1304.5
/MDO: P407.33, U1304.4
/MOBO_power/3V3_EN_1: R1505.2, U1502.6, U1504.6
/MOBO_power/3V3_EN_2: R1506.2, U1502.4, U1504.5
/MOBO_power/PWR_SEQ_EN: P407.15, U1504.3
/RX_UART: IC201.3, R101.2, R103.1, U301.5, U401.13
/SCL2: P407.19, R1306.2, R1311.2, R1413.1, R1413.2, TP1405.1, U1402.2, U1403.2
/SCLK: R701.1, R801.1, R901.1, R1102.1, R1201.2, U1304.18
/SDA2: P408.20, R1308.2, R1312.2, TP1406.1, U1402.3, U1403.3
/SDI: R703.1, R803.1, R903.1, R1104.1, R1109.2, R1203.2, U1304.17
/SDO: R702.2, R802.2, R902.2, R1103.2, R1202.1, U1304.16
/SEQ_ENABLE: R1507.2, U503.3, U703.3, U803.3, U903.3, U1103.3, U1203.3, U1303.3, U1504.4
/Sheet591E8E14/Vcc: IC201.7, IC201.20, JP201.2, R204.1
/Sheet5926AD0C/CH0: P501.2, U501.28
/Sheet5926AD0C/CH1: P502.2, U501.27
/Sheet5926AD0C/CH2: P503.2, U501.26
/Sheet5926AD0C/CH3: P504.2, U501.25
/Sheet5926AD0C/MUX_DATA: C506.2, R501.1, R502.1, U501.8
/Sheet5926AD0C/MUX_OUT: R501.2, U501.7, U502.3
/Sheet5926AD0C/Vref: C503.2, C508.1, U501.4, U503.5
/Sheet5926AD0C/~CS: IC201.16, U501.31
/Sheet592695A3/BBB_INT: P402.2, R402.2
/Sheet592695A3/BBB_INT_3V3: P408.14, R402.1, R404.1
/Sheet592695A3/BBB_ONOFF: P402.3, P402.4, P408.12
/Sheet592695A3/BBB_UART_EN: P407.41, U401.8
/Sheet592695A3/CAN1_HIGH: P409.15, P1304.1
/Sheet592695A3/CAN1_LOW: P409.17, P1304.2
/Sheet592695A3/CAN2_HIGH: P409.31, P1305.1
/Sheet592695A3/CAN2_LOW: P409.33, P1305.2
/Sheet592695A3/I2C1_SCL: P408.40, P1306.3, R1302.2
/Sheet592695A3/I2C1_SDA: P408.42, P1306.2, R1301.2
/Sheet592695A3/PWR_BUT: P401.1, R401.2
/Sheet592695A3/PWR_BUT_3V3: P408.30, R401.1, R403.1
/Sheet592695A3/SYS_OK: P403.1, P408.10
/Sheet592695A3/UART1_RX_BBB: P408.26, U401.3
/Sheet592695A3/UART1_TX_BBB: P408.24, U401.2
/Sheet592695A3/UART5_RX: P410.38, P411.2
/Sheet592695A3/UART5_TX: P409.37, P411.1
/Sheet592896E3/5V_ISO_0: C1406.1, P1302.4, R1309.1, R1310.1, U1402.8
/Sheet592896E3/5V_ISO_1: C1315.1, P1303.4, R1313.1, R1314.1, U1403.8
/Sheet592896E3/GND_ISO_0: C1406.2, P1302.1, U1402.5
/Sheet592896E3/GND_ISO_1: C1315.2, P1303.1, U1403.5
/Sheet592896E3/SSR_Data_0: P1302.2, R1310.2, TP1402.1, U1402.6
/Sheet592896E3/SSR_Data_1: P1303.2, R1314.2, TP1404.1, U1403.6
/Sheet592896E3/SSR_clock_0: P1302.3, R1309.2, TP1401.1, U1402.7
/Sheet592896E3/SSR_clock_1: P1303.3, R1313.2, TP1403.1, U1403.7
/Sheet59180297/Line0/AINP: C806.2, R704.2, R805.1, U801.8
/Sheet59180297/Line0/CH0: P801.5, R809.1
/Sheet59180297/Line0/CH1: P801.11, U801.27
/Sheet59180297/Line0/CH2: P801.17, U801.26
/Sheet59180297/Line0/CH3: P801.23, U801.25
/Sheet59180297/Line0/CH4: P801.29, U801.24
/Sheet59180297/Line0/CH5: P801.35, U801.23
/Sheet59180297/Line0/CH6: P801.41, U801.22
/Sheet59180297/Line0/CH7: P801.47, U801.21
/Sheet59180297/Line0/CH8: P801.44, U801.18
/Sheet59180297/Line0/CH9: P801.38, U801.17
/Sheet59180297/Line0/CH10: P801.32, U801.16
/Sheet59180297/Line0/CH11: P801.26, U801.15
/Sheet59180297/Line0/CH12: P801.20, U801.14
/Sheet59180297/Line0/CH13: P801.14, U801.13
/Sheet59180297/Line0/CH14: P801.8, U801.12
/Sheet59180297/Line0/CH15: P801.2, R806.2
/Sheet59180297/Line0/MUX_OUT: R704.1, U801.7, U802.3
/Sheet59180297/Line0/Vref: C803.2, C808.1, U801.4, U803.5
/Sheet59180297/Line1/AINP: C706.2, R705.1, U701.8
/Sheet59180297/Line1/CH0: P701.5, R709.1
/Sheet59180297/Line1/CH1: P701.11, U701.27
/Sheet59180297/Line1/CH2: P701.17, U701.26
/Sheet59180297/Line1/CH3: P701.23, U701.25
/Sheet59180297/Line1/CH4: P701.29, U701.24
/Sheet59180297/Line1/CH5: P701.35, U701.23
/Sheet59180297/Line1/CH6: P701.41, U701.22
/Sheet59180297/Line1/CH7: P701.47, U701.21
/Sheet59180297/Line1/CH8: P701.44, U701.18
/Sheet59180297/Line1/CH9: P701.38, U701.17
/Sheet59180297/Line1/CH10: P701.32, U701.16
/Sheet59180297/Line1/CH11: P701.26, U701.15
/Sheet59180297/Line1/CH12: P701.20, U701.14
/Sheet59180297/Line1/CH13: P701.14, U701.13
/Sheet59180297/Line1/CH14: P701.8, U701.12
/Sheet59180297/Line1/CH15: P701.2, R706.2
/Sheet59180297/Line1/MUX_OUT: U701.7, U702.3
/Sheet59180297/Line1/Vref: C703.2, C708.1, U701.4, U703.5
/Sheet59180297/Line2/AINP: C906.2, R804.2, R905.1, U901.8
/Sheet59180297/Line2/CH0: P901.5, R909.1
/Sheet59180297/Line2/CH1: P901.11, U901.27
/Sheet59180297/Line2/CH2: P901.17, U901.26
/Sheet59180297/Line2/CH3: P901.23, U901.25
/Sheet59180297/Line2/CH4: P901.29, U901.24
/Sheet59180297/Line2/CH5: P901.35, U901.23
/Sheet59180297/Line2/CH6: P901.41, U901.22
/Sheet59180297/Line2/CH7: P901.47, U901.21
/Sheet59180297/Line2/CH8: P901.44, U901.18
/Sheet59180297/Line2/CH9: P901.38, U901.17
/Sheet59180297/Line2/CH10: P901.32, U901.16
/Sheet59180297/Line2/CH11: P901.26, U901.15
/Sheet59180297/Line2/CH12: P901.20, U901.14
/Sheet59180297/Line2/CH13: P901.14, U901.13
/Sheet59180297/Line2/CH14: P901.8, U901.12
/Sheet59180297/Line2/CH15: P901.2, R906.2
/Sheet59180297/Line2/MUX_OUT: R804.1, U901.7, U902.3
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

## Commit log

2016-11-04 Initial commit of full electrical. Still need to add Front and Back Board KiCad projects
    [CenterBoard.sch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]
2016-11-04 Reorganized folders such that the final version of a Rev has a folder, with subfolders for each board, and the boards of the current working rev are kept in the root directory.
    [CenterBoard.sch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]
2016-11-08 Initial commit of Main Power Board. Design of 24V and 5V regulators complete. Need to design surround circuitry and add safety devices.
    [24V_regulator.sch, 5V_regulator.sch, MainPowerBoard.sch]
2016-11-08 Added battery interface to Main Power Board schematic (the indicator light circuit still needs modification and fuses/jumpers need to be spec'd and chosen)
    [5V_regulator.sch, BattProtect.sch, MainPowerBoard.sch]
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2016-11-14 Updated MainPowerBoard with simplified battery circuit and interface to AC-DC converter (now planned to be off-board)
    [24V_regulator.sch, 5V_regulator.sch, BattProtect.sch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]
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2016-11-18 Created on/off switch - still needs delay circuit (RC) and Schmitt Trigger
    [24V_regulator.sch, 5V_regulator.sch, BattProtect.sch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]
2016-11-18 Completed design of On/Off Switch. Ready for layout pending last few component choices and analysis of On/Off Switch analysis.
    [MainPowerBoard.sch, OnOffSwitch.sch]
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2016-11-21 Rework of battery board schematic
    [BatteryBoard.sch, Bottom Capacitors and Resistors.sch, Bottom Fets and Resistors.sch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]
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2016-11-22 Changes from schematic review of Main Power Board with Manny, Rohan, and Luke
    [BattProtect.sch, BatteryBoard.sch, OnOffSwitch.sch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]
2016-11-26 Changed annotations for entire schematic. Added footprint library. Added initial PCB. Removed TP connections to ground
    [24V_regulator.sch, 5V_regulator.sch, BattProtect.sch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]
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2016-11-27 Updated 24V regulator circuits with new part and design (TI LMR13060). Updated On/Off Switch to use EN inputs on regulators instead of low-side FETs to turn on/off system. TODO: Update 5V regulator
    [24V_regulator.sch, 5V_regulator.sch, BattProtect.sch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]
2016-11-28 Updated 5V regulator. Added 0Ohm resistors for all signals. Added protection zeners and diodes on battery inputs and on regulator outputs. TODO: Finish component selection.
    [24V_regulator.sch, 5V_regulator.sch, BattProtect.sch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]
2016-11-29 Updated MainPowerBoard with various component footings. Added protective circuitry. Revised minor design elements.
    [24V_regulator.sch, 5V_regulator.sch, BattProtect.sch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]
2016-11-29 Added all standard footprints to components. Finalized protection circuitry and indicator circuits.
    [24V_regulator.sch, 5V_regulator.sch, BattProtect.sch]
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2016-12-01 Chose new, smaller connectors and created footprints. Began populating layout (it's a MESS). TODO: Make layout not a mess.
    [MainPowerBoard.kicad_pcb, MainPowerBoard.sch, OnOffSwitch.sch]
2016-12-02 Began MainPowerBoard layout. Decided on final size of 7x7. Placed battery connectors. Finalized almost all footprints. Laid out one regulator circuit. TODO: Finish regulator layout; duplicate it; pic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
    [24V_regulator.sch, 5V_regulator.sch, BattProtect.sch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]
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2016-12-05 Continued working on layout. Fixed LED indicators for ON/OFF controller.
    [24V_regulator.sch, 5V_regulator.sch, BattProtect.sch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]
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2016-12-06 Continued layout of Main Power Board. TODO: find new pushbutton, replace VCC_BATT routing with power plane (AFTER routing signals)
    [24V_regulator.sch, 5V_regulator.sch, BattProtect.sch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]
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2016-12-07 Cleaned up layout. Ran DRCs (all passed). Neatened up silkscreen. Exported Gerbers for quote from 4pcb with fast turnaround and DFM check.
    [24V_regulator.sch, 5V_regulator.sch, MainPowerBoard.kicad_pcb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]
2016-12-07 Modified footprint of on-diodes to match their spec. Adjusted On/Off linear regulator to be 5V instead of 12V in order to better meet some pin max voltages.
    [24V_regulator.sch, BattProtect.sch, MainPowerBoard.kicad_pcb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]
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2016-12-09 Archived Rev_001 MainPowerBoard. Updated layout for pending Rev_002 release. Updated schematic components where necessary.
    [24V_regulator.sch, 5V_regulator.sch, BattProtect.sch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]
2016-12-11 Added the power switching device and wiring between the pod batteries and backup batteries
    [IndCkt.sch, LEDBoard.sch, _saved_SOT2.sch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]
2016-12-11 Made some updates to battery board schematic. Inching our way to custom battery boards.
    [BatteryBoard.sch, bom_pcb.csv, bq76930AFE.sch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]
2016-12-12 Began selecting components for Battery Board based on bq76930 EVM BOM. Also verified that all circuits matched the EVM schematic and also the bq76930 datasheet.
    [BatteryBoard.sch, bq76930AFE.sch, bq78350Companion.sch]
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2016-12-13 Selected all components for battery board. Ready for schematic review. Pursuing layout tomorrow.
    [BatteryBoard.kicad_pcb, BatteryBoard.sch, bq76930AFE.sch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]
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2016-12-16 added more modules to the Led board and put in the circuit for the cool switch and the Led that goes along with it. Also made some more changes to the sensors and which ones we are going to have
    [IndCkt.sch, LEDBoard.sch, powerswitch.sch]
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2016-12-23 Updated LED board with conditioning circuit
    Conditioning circuit for merkls psi added as well as the pcb layout nearly completely done. added all the logic resistors.
    [IndCkt.sch, LEDBoard.kicad_pcb, LEDBoard.sch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]
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2017-01-02 Add Correct Motherboard to git
    [3.sch, 3_3V_reg.sch, 4V_Reg.sch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]
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2017-01-08 Corrected problem with Pusher Protection Board. Updated both schematic and layout and regenerated and zipped Gerbers. Ready for fab.
    [BrakeInterlock.sch, PusherDelay.sch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]
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2017-03-30 Fixed Component Naming Error
    On the 8th 24V rail, one of the outputs should be conntected to "Low
    pressure bleed valve (relay panel)" instead of "High pressure bleed
    valve (relay panel)"
    [24V_regulator.sch, 5V_regulator.sch, BattProtect.sch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]
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2017-05-02 Adding Changes to the SSR Board such as a change on the PCB allocating for the correct amount of channels as well as adding the control circuitry for the MPYE’s to the schematic. So changes on the: s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
    [SSRBoard-B.Cu.gbr, SSRBoard-B.Mask.gbr, SSRBoard-B.Paste.gbr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]
2017-05-07 Deleted some of the unnecessary circuits for the relays that won’t be used anymore since we will have two boards now.
    [SSRBlock.sch, SSRBoard.kicad_pcb, SSRBoard.sch]
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2017-05-10 Fixed grounding of bat output and connected missing ground connection on LTC chip
    [BattProtect.sch, MainPowerBoard.kicad_pcb, MainPowerBoard.sch]
2017-05-15 Finalized Power Selector Circuit
    Replaced Schottky Diodes with Ideal Diodes. Converted 8th 24V Rail to
    second 5V rail.
    [24V_regulator.sch, 5V_regulator.sch, BattProtect.sch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]
2017-05-17 Added the xtr117 to the schematic but I still need to make the footprint for it since the one on kicad is wrong.
    [SSRBoard.sch]
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2017-05-25 Completely started over. There's a ton of changes. Some highlights are: isolation for I2C, demux to allow CS to work for the 8 SPI ADCs, and general cleanliness compared to V1. Still transcribing not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
    [Motherboard.sch]
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2017-06-07 Converted back to 8 24V rails on MPB, fixed NC pins on THBO schematic
    [24V_regulator.sch, 5V_regulator.sch, MainPowerBoard.kicad_pcb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]
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2017-07-10 SSR Board 2.1.2
    James’s advice has been taken
    [SSRBlock.sch, SSRBoard.kicad_pcb, SSRBoard.sch]
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2017-07-12 Added fuse to board; broke timers into hierarchical sheets; began choosing components and populating footprints
    [BatteryBoard.sch, DischargeTimer.sch, Pre-ChargeTimer.sch]
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2017-07-14 Fixed minor error in Main FET timing circuit
    [BatteryBoard.sch, DischargeTimer.sch]
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2017-07-17 Fixed component footprints; finalized silkscreen; output Gerbers
    [BatteryBoard-B.Cu.gbr, BatteryBoard-B.Mask.gbr, BatteryBoard-B.Paste.gbr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]
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2017-07-30 Revert "Merge branch 'master' of https://github.com/ParadigmHyperloop/electrical"
    This reverts commit 47d31288c6bddacbab6660df29785a0729d95fbe, reversing
    changes made to 90896756f2378821ec6625d68bade529b6c4440f.
    [BatteryBoard.sch, DischargeTimer.sch, FinalLED.kicad_pcb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]
2017-07-30 Pushing up James' changes
    [BatteryBoard.sch, DischargeTimer.sch, Pre-ChargeTimer.sch]
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2017-10-03 Version 2. Board interfaces with an Arduino to control an onboard buzzer and external LEDs. Some silkscreen is missing
    [IndCkt.sch, LEDBoard.kicad_pcb, LEDBoard.sch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]
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2018-01-29 Fixed all incorrect trace size issues. Passed DRC. Added extra 5V header. Began labeling connectors with human readble names. Changed all through hole GND pins to rectangular pads instead of circular
    [node.kicad_pcb, power_sub.sch]
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2018-07-01 fixed and routed driver spi issue
    Added new rx/tx bus for solenoid driver. Routed it too. Nice.
    [24V_sub.sch, 3V3_sub.sch, 5V0_sub.sch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]
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2018-07-23 Fixed issue with kicad
    [3V3_sub.sch, _saved_3V3_sub.sch, _saved_USB_power_sub.sch]
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2021-11-10 Update Readme.md
    https://forum.kicad.info/t/warning-avoid-all-links-to-kicad-pcb-org-use-kicad-org/31521

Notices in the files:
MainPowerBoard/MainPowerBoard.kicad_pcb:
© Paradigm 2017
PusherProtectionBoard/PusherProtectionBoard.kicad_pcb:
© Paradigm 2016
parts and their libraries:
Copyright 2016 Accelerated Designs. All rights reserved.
